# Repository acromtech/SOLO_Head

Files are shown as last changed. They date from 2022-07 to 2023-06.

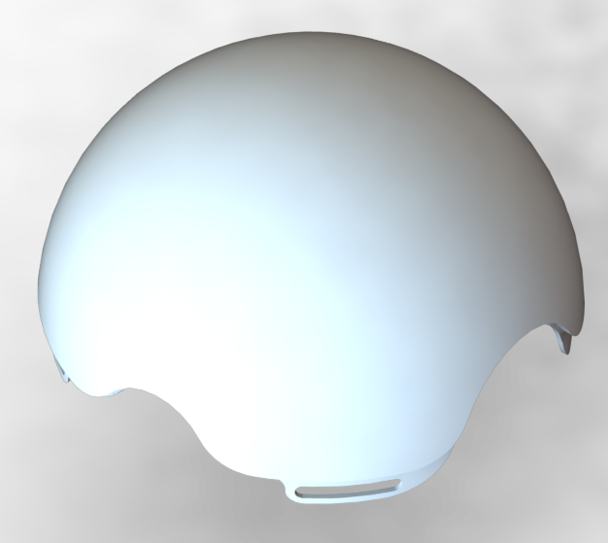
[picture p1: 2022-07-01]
SOLO_HEAD_1DOF_V6/IMAGES/Head_Top.png

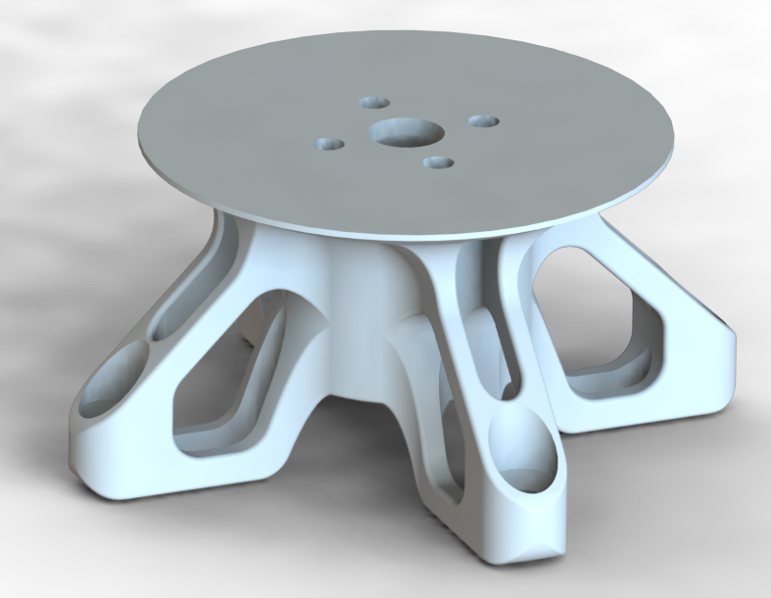
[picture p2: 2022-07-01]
SOLO_HEAD_1DOF_V6/IMAGES/SH06-Head_Stand.png

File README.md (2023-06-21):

# SOLO_Head

## Assembly
Solo_Head
<br>*Note : Equations can be used to re-size head diameter*

## Design Parts
| CAO | Print | Printing time | Name | Filament | Comment |
|:---:|:---:|---|---|---|---|
|  |  | 9h | 1x Head_Top | ABS | 45° touching buildplate supports required (use soluble supports is better) |
|  | | 1min | 1x Head_Joint | Neoprene | made with laser cutter machine |
|  || 33min | 2x Microphone_Joint | TPU | 45° touching buildplate supports required (use soluble supports is better) |
|  || 20min | 4x Camera_Spacer<br>4x CM4_Spacer<br>8x uDriver_Spacer | ABS | No support required |
|  |  | 1h | 1x Board_Mount | ABS | No support required |
|  |  | 5min | 1x End_Stop | ABS | No support required |
|  | | 1h30 | 1x Encoder_Mount | ABS | No support required |
|  |  | 20min | 1x Encoder_Adaptator | ABS | No support required |
|  |  | 12h | 1x Head_Bottom | ABS | 45° touching buildplate supports required (use soluble supports is better) |
|  || 4h | 1x Head_Stand | ABS | No support required but print with soluble support is better |

## Generic Parts
| Screen | Reference | Link | Comment |
|:---:|---|---|---|
||1x 6700-2RS ball bearing<br>Ø10xØ15x4mm|[123Roulement](https://www.123roulement.com/roulements-6700-2RS)|To link "Encoder_Mount" and "Encoder_Adaptator" design parts|
||8x TCHC M3x8 Screw|[Fixnvis](https://www.visseriefixations.fr/vis-a-six-pans-creux/tete-fraisee-hexagonale-creuse/inox-a4/tfhc-m3x8-inox-a4-ef-din-7991.html)|To link "Encoder_Mount" design part and the motor<br>To link "Encoder_Mount" and "Head_Bottom" design parts|
||4x TCHC M2.5x20 Screw|[Fixnvis](https://www.visseriefixations.fr/vis-a-six-pans-creux/tete-fraisee-hexagonale-creuse/inox-a4/tfhc-m2-5x20-inox-a4-din-7991.html)|To link "Board_Mount" with spacers and "Head_Bottom" design parts|
||1x AEDB-9140-A13 Broadcom Encoder|[RS](https://fr.rs-online.com/web/p/codeurs/7967806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)|/|
||1x GB4106 Tmotor motor|[Hexadrone](https://hexadrone.fr/gamme-gimbal-nacelle/509-moteur-brushless-nacelle-gb4106-tmotor-6971360351184.html)|/|
||1x Arducam 2MP Global Shutter OG02B10 Pivariety camera module |[Robotshop](https://www.robotshop.com/be/fr/module-camera-couleur-arducam-2mp-global-shutter-og02b10-pivariety.html)|/|
||1x ArduCam M12 camera lens (6pcs)|[Robotshop](https://www.robotshop.com/be/fr/kit-objectif-arducam-m12-pour-camera-hq-20-180deg-6pcs.html)|/|
||1x CM4 Raspberry Pi|[Kubii](https://www.kubii.fr/cartes-raspberry-pi/3086-raspberry-pi-compute-module-4-3272496302952.html)|/|
||2x Microphone module|/|Electronic CAD are in the repository "hardware"|
||2x uDriver board||[ODRI repository](https://github.com/open-dynamic-robot-initiative/open_robot_actuator_hardware/blob/master/electronics/micro_driver_electronics/README.md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)|
||2x DF13-5S-1.25C Hirose connector|[RS components](https://fr.rs-online.com/web/p/boitiers-de-connecteurs-pour-circuits-imprimes/1113616)|To link uDriver and communication cables<br>To link CM4 Raspberry Pi and communication cables|
||1x DF13-5P-1.25DS Hirose connector|[RS components](https://fr.rs-online.com/web/p/embases-circuits-imprimes/7793529)|To change encoder connector|
||1x DF13-5P-1.25DSA Hirose connector|[RS components](https://fr.rs-online.com/web/p/embases-circuits-imprimes/5037912)|To link head CM4 Raspberry Pi shield communication cables to body Raspberry Pi communication cables|
||1x RE-6619107 XT30U 2 mm Reely Male  connector|[Conrad](https://www.conrad.fr/p/reely-re-6619107-fiche-male-pour-batterie-xt30u-2-mm-femelle-doree-a-souder-1-pcs-2206369)|To link power cables to uDriver board|
||1x RE-6619104 XT30U 2 mm Reely Female connector|[Conrad](https://www.conrad.fr/p/reely-re-6619107-fiche-male-pour-batterie-xt30u-2-mm-femelle-doree-a-souder-1-pcs-2206369)|To link power cables to power board (on SOLO body)|
||1x Kabeltronik 160110009-1 1mm² Black Power Wire|[Conrad](https://www.conrad.com/p/kabeltronik-160110009-1-strand-lify-1-x-1-mm-black-sold-per-metre-323735)|To power uDriver board|
||1x Kabeltronik 160110008 1mm² Red Power Wire|[Conrad](https://www.conrad.fr/p/fil-de-cablage-lify-kabeltronik-160110008-1-1-x-1-mm-rouge-marchandise-vendue-au-metre-323734)|To power uDriver board|
||1x 10 way 3M 3302-10 100FT communication cables |[RS components](https://fr.rs-online.com/web/p/cables-en-nappe/1055281)|To link encoder and uDriver (5 way)<br>To link CM4 Raspberry Pi and uDriver (5 way)|
||1x DF13-2630SCF 0.12mm² Hirose DF13 Crimp Terminals|[RS components](https://fr.rs-online.com/web/p/cables-en-nappe/1055281)|To link communication cables with DF13-5S-1.25C Hirose connector|
||1x DF13-TB2630HC Hirose Crimping Tool for DF13 Crimp Terminals |[RS components](https://fr.rs-online.com/web/p/cables-en-nappe/1055281)|To link communication cables with DF13-5S-1.25C Hirose connector|

## Next Version (V7)
To reduce mass, clean print, and keep design apparence. I realize some modifications on the V6 design :
* Delete "Head_Joint" neoprene gasket and chamfer "Head_Bottom" and "Head_Top" parts to simplify the model and clean model surface.
* Design a new "Head_Stand" to link the SOLO's head to SOLO's body.
* Delete "Microphone_Joint" and integrate a screwing system on "Head_Bottom" to simplify the model. To limit microphone noise, generic O-rings are positioned on the screw.
* Upgrade clips shape to limit printing supports.

## License
BSD 3-Clause License

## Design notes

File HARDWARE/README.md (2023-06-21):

# Hardware

## Features
Quantity|Reference|Voltage [V]|Intensity [A]|Detail
---|---|---|---|---|
1|[SLS X-Cube 850mAh lithium polymer batteries](https://github.com/open-dynamic-robot-initiative/open_robot_actuator_hardware/blob/master/mechanics/quadruped_robot_12dof_v1.1/README.md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)|24(2x3S)|30C continous = 2 x 30 x 0.85 = 51<br>60C burst = 2 x 60 x 0.85 = 102 |/|
1|[uDriverv2](https://github.com/open-dynamic-robot-initiative/open_robot_actuator_hardware/tree/master/electronics/micro_driver_electronics)|5-32|/|/|
2|[IPower GM2804 (+ AS5048A encoder)](https://www.robotshop.com/ca/fr/moteur-cardan-ipower-gm2804-avec-encodeur-as5048a.html)|10|0.07-5|Hollow shaft diameter : 5.7mm <br> [Drawings](https://user-images.githubusercontent.com/103576080/168556596-d6f692c8-2cbd-48c1-b92e-5072b6c10471.jpg) <br> Resistance : 5.57Ω|
2|[AEDB-9140-A13 optical encoder](https://fr.rs-online.com/web/p/codeurs/7967806)|(-0.5)-7|0.001-0.018|/|
2|[I2S MEMS (MicroElectroMechanical Systems) microphone for Raspberry Pi](https://makersportal.com/shop/i2s-mems-microphone-for-raspberry-pi-inmp441)|/|/|/|
1|[Arducam OG02B10 2MP Global Shutter color camera module](https://www.arducam.com/product/arducam-2mp-og02b10-global-shutter-color-camera-modules-for-raspberry-pi/)|/|/|/|
1 | Raspberry Pi CM4|5|3|/|

## Minimum power wires section
Raspberry Pi 4 maximum intensity + Motor maximum intensity = 8A

>S = (ρ x 2L x I)/U’ = 0.021 x 2 x 8 / (24 x 0.3) = 0.46mm²<br>S = (ρ x 2L x I)/U’ = 0.021 x 2 x 8 / (48 x 0.3) = 0.23mm²

Unit | Detail |
--- | --- |
ρ | coper resistance = 0.021|
L | cable length (go+back)|
I | system intensity|
U' | voltage drop = system voltage x 3%|

So, for a 24V battery voltage, a battery intensity max of 8A and a 1m cable length (2m in the up table) a 0.5mm² cable section be sufficient. Usualy 0.5mm² section cable have ~Ø2.6mm outer diameter. 
>Currently 1mm² section are used on SOLO quadruped robot to power legs uDriverv2.

## Raspberry Pi communication wires
Self-made ethernet wire with 4 connections|Robot interface wire|
---|---|
ethernet_connector | connection_wire_2
> Four RS 180-6028 wires (0.14mm²/~Ø1.5mm) are fixed to the ethernet connector ([more informations](https://github.com/open-dynamic-robot-initiative/open_robot_actuator_hardware/blob/master/electronics/details/details_wiring.md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))

## SOLO head wire
>Hollow shaft superficy : π(5.7/2)² = 25.52mm² <br> Wire superficy : 2π(2.6/2)² + 4π(1.5/2)² = 17.69mm²

17.69mm² < 25.52mm² => OK

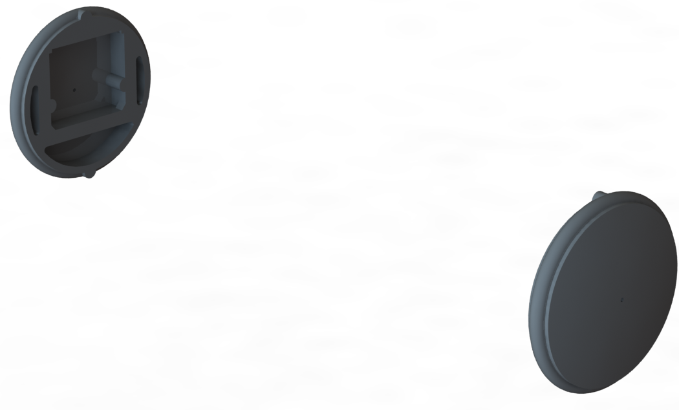
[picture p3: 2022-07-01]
SOLO_HEAD_1DOF_V6/IMAGES/Microphone_Joint.png

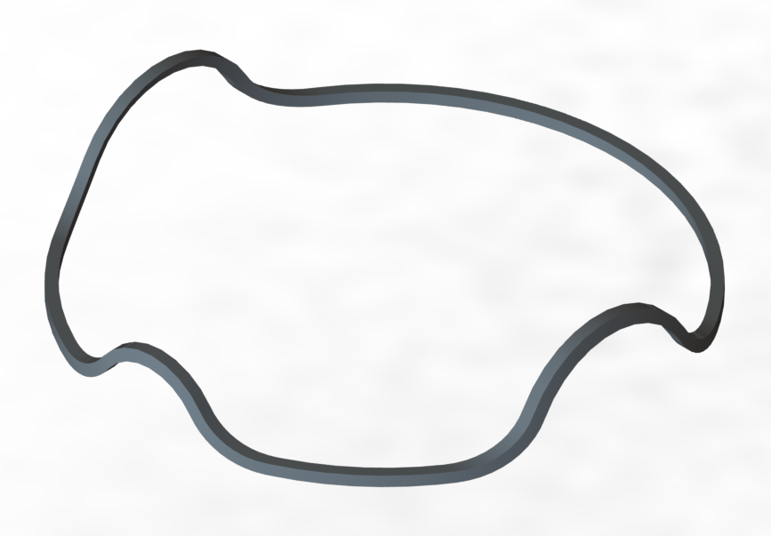
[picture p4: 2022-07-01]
SOLO_HEAD_1DOF_V6/IMAGES/Joint.png

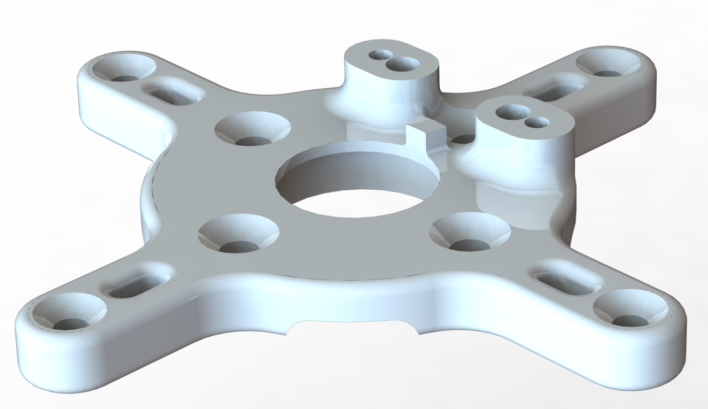
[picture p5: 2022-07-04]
SOLO_HEAD_1DOF_V6/IMAGES/Encoder_Mount.png

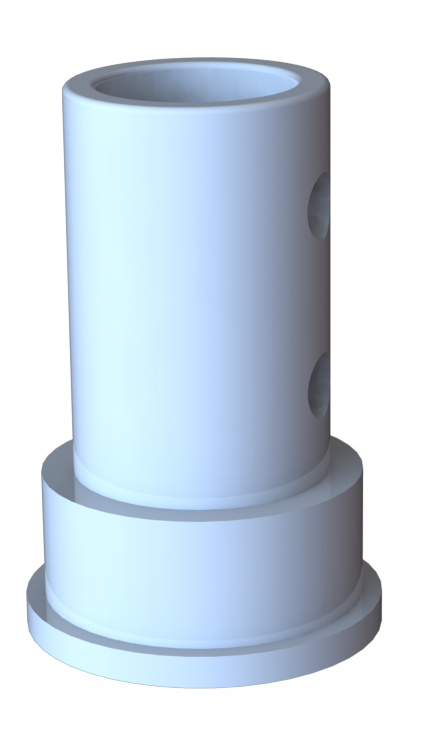
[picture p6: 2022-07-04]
SOLO_HEAD_1DOF_V6/IMAGES/Encoder_Adaptator.png

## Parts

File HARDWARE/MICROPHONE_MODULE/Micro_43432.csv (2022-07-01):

Id | Designator | Package | Quantity | Designation | Supplier and ref
1 | C1 | C_0402_1005Metric | 1 | 0.1u
2 | J1 | Hirose_DF13-06P-1.25DSA_1x06_P1.25mm_Vertical | 1 | Conn_01x06_Female
3 | R1 | R_01005_0402Metric_Pad0.57x0.30mm_HandSolder | 1 | 100k
4 | K1 | MIC_ICS-43432 | 1 | ICS-43432

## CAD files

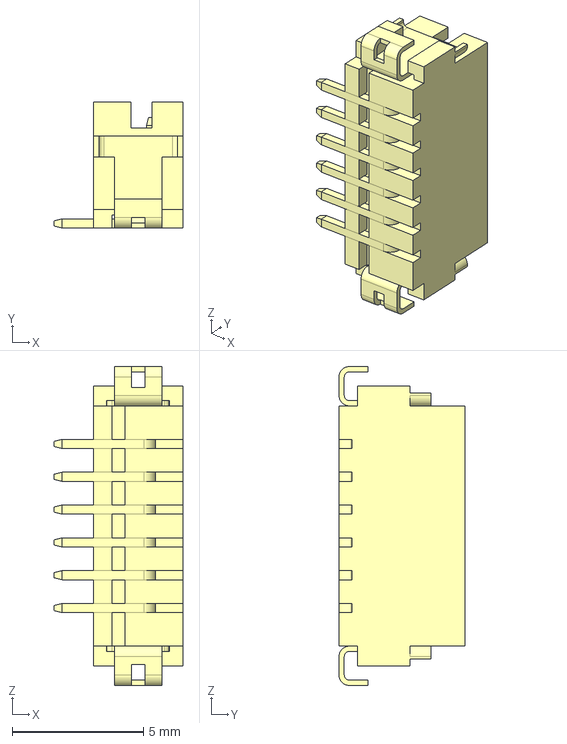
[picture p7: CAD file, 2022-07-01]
HARDWARE/MICROPHONE_MODULE/DF13C-6P-1.25V(21)_CL0536-0405-3-21_3DDrawing_STEP_0001217384S/WNCW-1600327.stp
4.90 x 4.80 x 12.2 mm

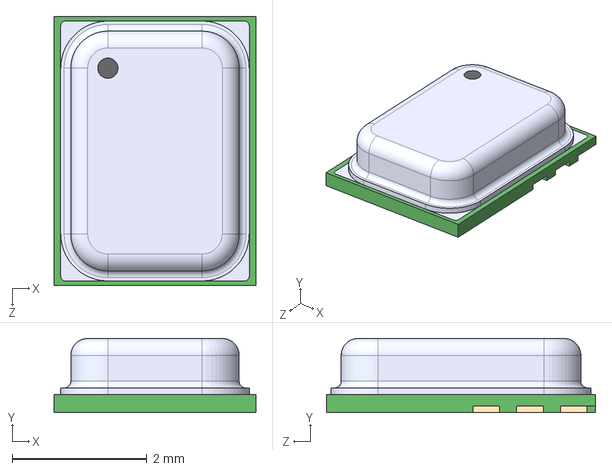
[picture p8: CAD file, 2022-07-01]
HARDWARE/MICROPHONE_MODULE/ICS-43432/ICS-43432.step
3.00 x 1.10 x 4.00 mm

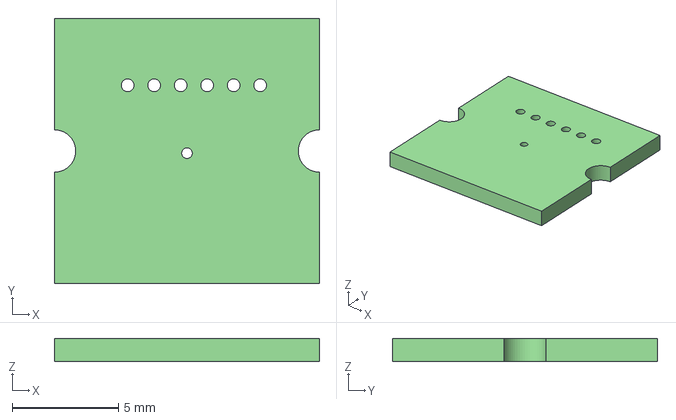
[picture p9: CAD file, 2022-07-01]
HARDWARE/MICROPHONE_MODULE/Micro_43432.step
12.5 x 12.5 x 1.09 mm

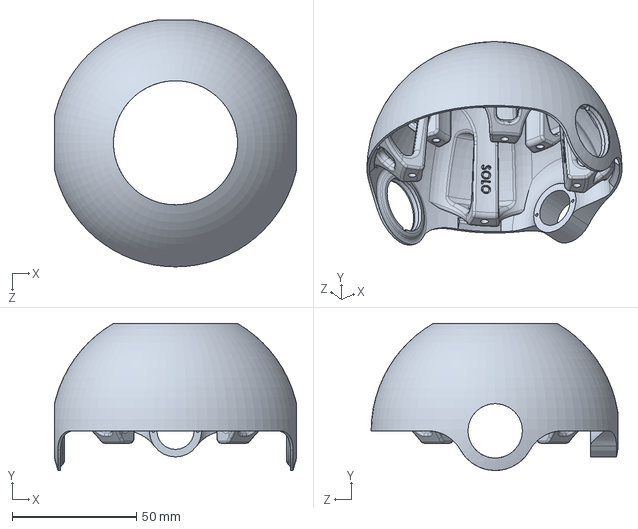
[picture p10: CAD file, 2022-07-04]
SOLO_HEAD_1DOF_V6/SOLIDWORKS_ASSEMBLY/SH06-Head_Bottom.SLDPRT
97.5 x 59.3 x 99.4 mm

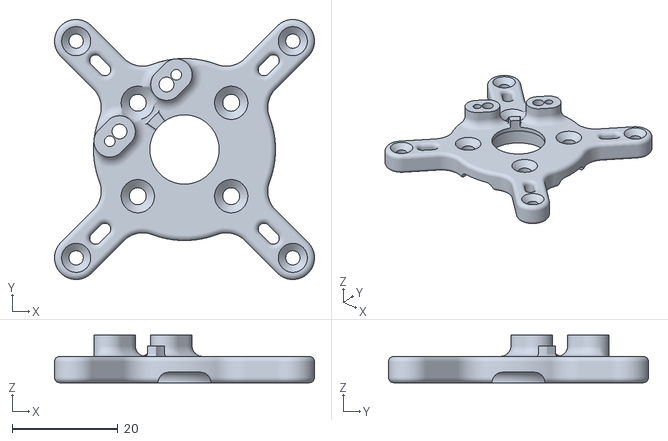
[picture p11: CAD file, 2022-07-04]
SOLO_HEAD_1DOF_V6/STL/SH06-Encoder_Mount_V2.STL
49.2 x 49.2 x 9.00

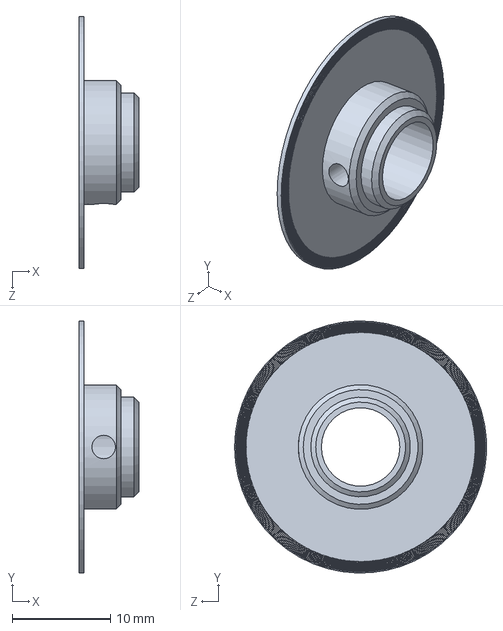
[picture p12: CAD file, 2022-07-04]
SOLO_HEAD_1DOF_V6/SOLIDWORKS_ASSEMBLY/SH06-zz_AEDB-9140-A13_broadcom_encoder_wheel.SLDPRT
6.08 x 25.7 x 25.7 mm

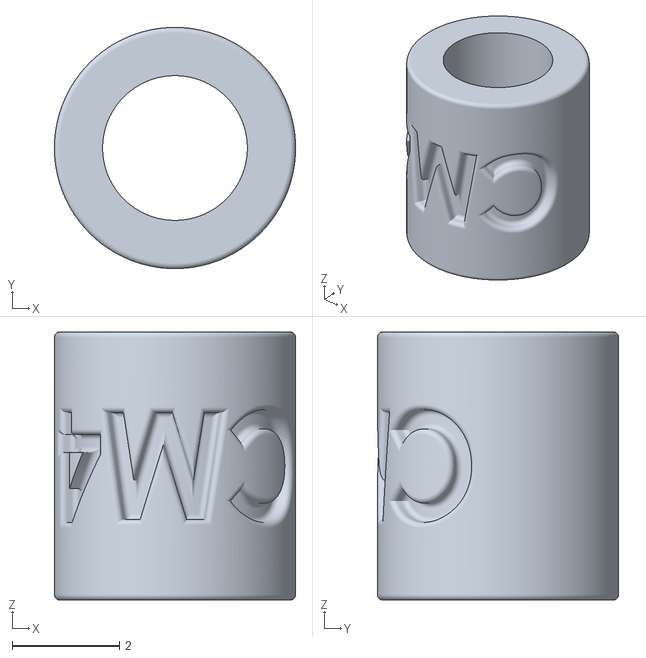
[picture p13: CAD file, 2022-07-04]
SOLO_HEAD_1DOF_V6/STL/SH06-Shield_CM4_Spacer.STL
4.50 x 4.50 x 5.00

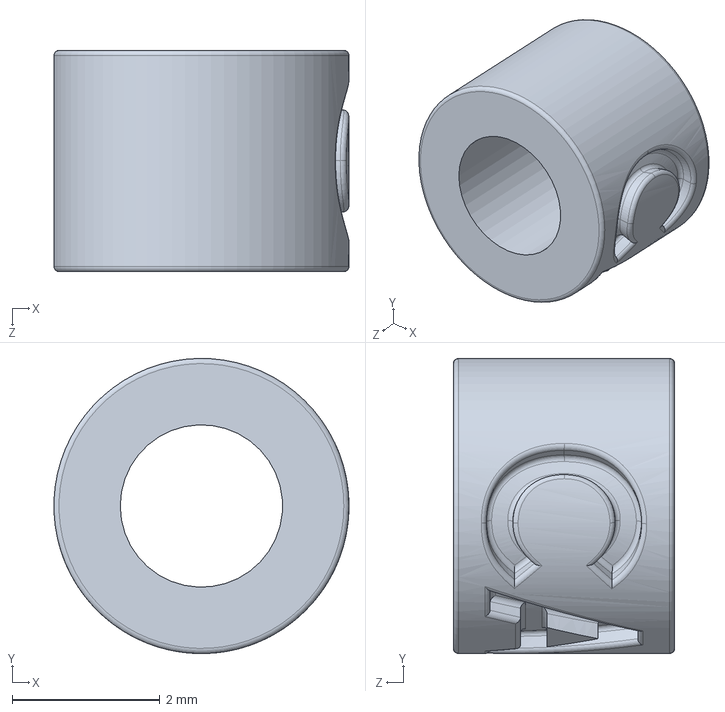
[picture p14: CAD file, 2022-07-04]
SOLO_HEAD_1DOF_V6/SOLIDWORKS_ASSEMBLY/SH06-Camera_Module_Spacer.SLDPRT
4.00 x 4.00 x 3.00 mm

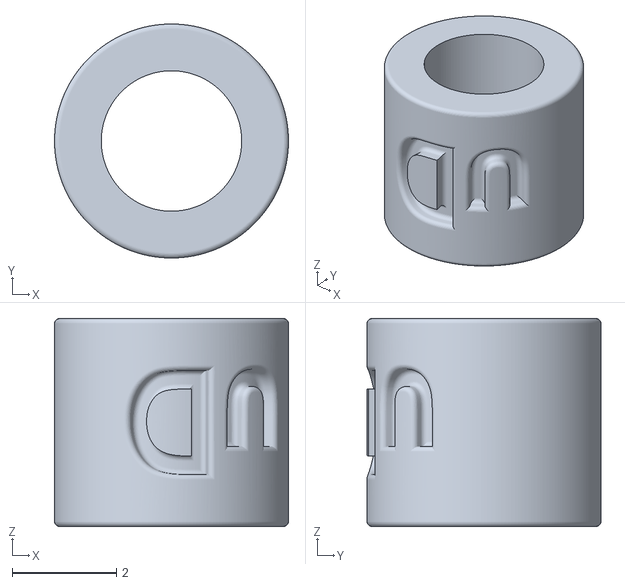
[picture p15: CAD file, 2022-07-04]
SOLO_HEAD_1DOF_V6/STL/SH06-uDriver_Spacer.STL
4.50 x 4.50 x 4.00

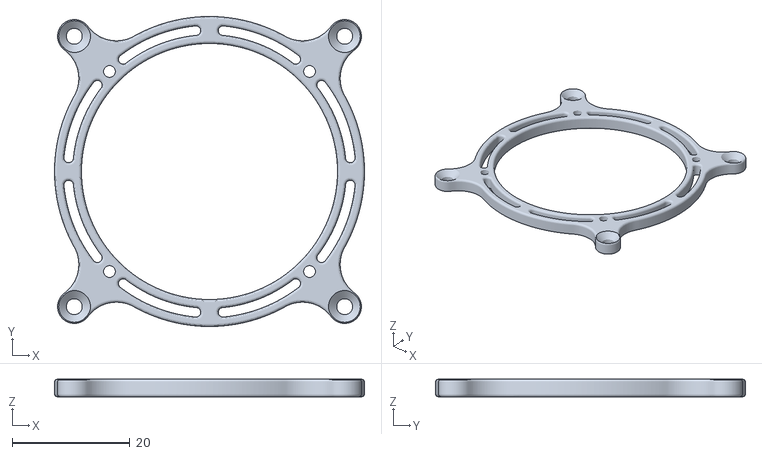
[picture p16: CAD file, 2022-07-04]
SOLO_HEAD_1DOF_V6/STL/SH06-Boards_Mount.STL
52.7 x 52.7 x 3.00

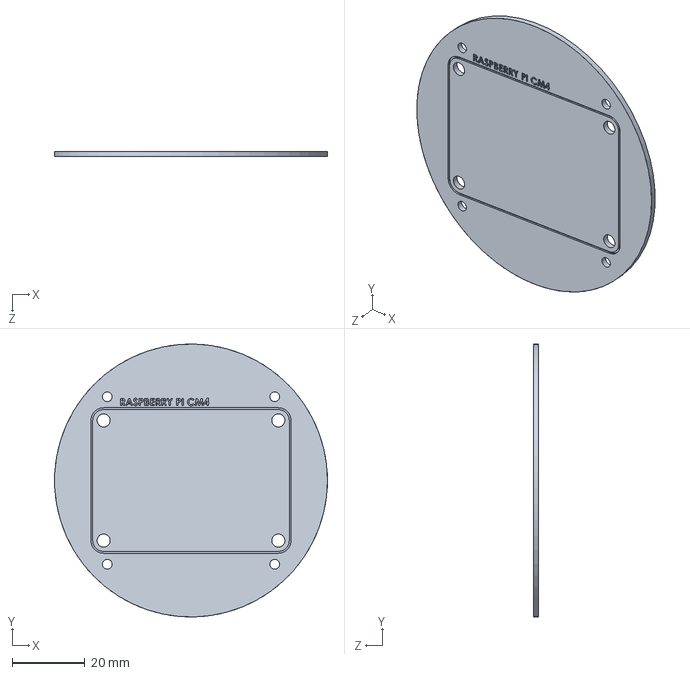
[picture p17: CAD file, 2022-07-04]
SOLO_HEAD_1DOF_V6/SOLIDWORKS_ASSEMBLY/SH06-Shield_CM4_Footprint.SLDPRT
75.0 x 75.0 x 1.50 mm

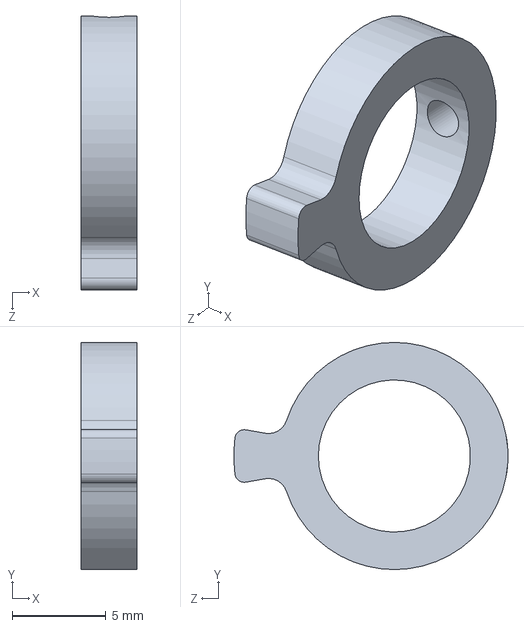
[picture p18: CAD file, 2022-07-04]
SOLO_HEAD_1DOF_V6/SOLIDWORKS_ASSEMBLY/SH06-End_Stop.SLDPRT
3.00 x 12.1 x 14.6 mm

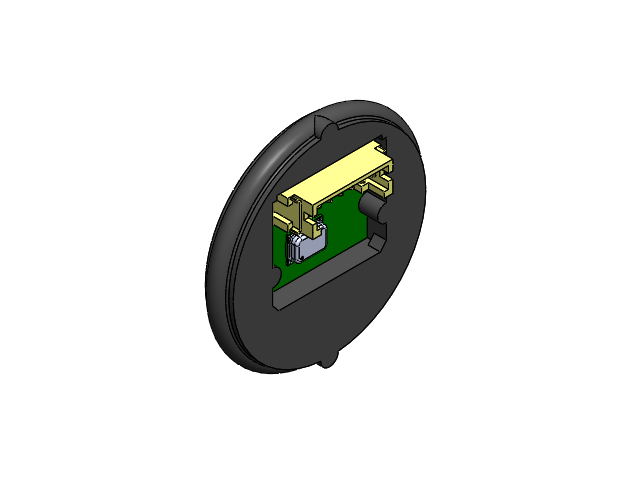
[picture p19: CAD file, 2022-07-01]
SOLO_HEAD_1DOF_V6/SOLIDWORKS_ASSEMBLY/SH06-01-MICROPHONE_MODULE_V3.SLDASM
SH06-Microphone_Joint_V3
SH06-zz_laas_microphone_v3

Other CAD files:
SOLO_HEAD_1DOF_V6/SOLIDWORKS_ASSEMBLY/SH06-uDriver_Spacer.SLDPRT
SOLO_HEAD_1DOF_V6/STL/SH06-Shield_CM4_Footprint.STL
SOLO_HEAD_1DOF_V6/STL/SH06-Camera_Module_Spacer.STL
SOLO_HEAD_1DOF_V6/SOLIDWORKS_ASSEMBLY/SH06-Encoder_Mount_V2.SLDPRT
HARDWARE/MICROPHONE_MODULE/Micro_43432_no_screw.step
SOLO_HEAD_1DOF_V6/DXF/SH06-Head_Joint_V4.DXF
SOLO_HEAD_1DOF_V6/SOLIDWORKS_ASSEMBLY/SH06-Boards_Mount.SLDPRT
SOLO_HEAD_1DOF_V6/SOLIDWORKS_ASSEMBLY/SH06-Encoder_Adaptator_V2.SLDPRT
SOLO_HEAD_1DOF_V6/SOLIDWORKS_ASSEMBLY/SH06-Head_Joint_V4.SLDPRT
SOLO_HEAD_1DOF_V6/SOLIDWORKS_ASSEMBLY/SH06-Head_Stand.SLDPRT
SOLO_HEAD_1DOF_V6/SOLIDWORKS_ASSEMBLY/SH06-Head_Top_V2.SLDPRT
SOLO_HEAD_1DOF_V6/SOLIDWORKS_ASSEMBLY/SH06-Microphone_Joint_V3.SLDPRT
SOLO_HEAD_1DOF_V6/SOLIDWORKS_ASSEMBLY/SH06-Shield_CM4_Spacer.SLDPRT
SOLO_HEAD_1DOF_V6/SOLIDWORKS_ASSEMBLY/SH06-zz_AEDB-9140-A13_broadcom_encoder.SLDPRT
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

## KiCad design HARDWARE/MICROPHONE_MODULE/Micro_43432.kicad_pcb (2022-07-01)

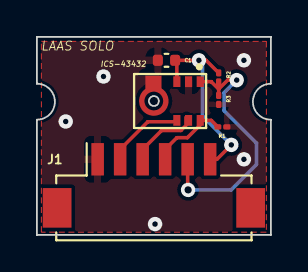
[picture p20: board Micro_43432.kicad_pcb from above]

Board: 2 copper layers, 13.0 x 11.0 mm, 6 parts (0 on the bottom side), 6 nets.

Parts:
C1: 0.1u; C_0402_1005Metric
J1: Conn_01x06_Female; Hirose_DF13C_CL535-0406-3-51_1x06-1MP_P1.25mm_Vertical
K1: ICS-43432; MIC_ICS-43432
R1: 100k; R_01005_0402Metric
R2: NC; R_01005_0402Metric
R3: 0; R_01005_0402Metric

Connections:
/LR: J1.5, K1.1 (LR), R2.2, R3.1
/SCK: J1.3, K1.6 (SCK)
/SD: J1.4, K1.7 (SD), R1.1
/WS: J1.2, K1.5 (WS)
GND: C1.2, J1.1, K1.2 (CONFIG), K1.4 (GND), R1.2, R3.2
VDD: C1.1, J1.6, K1.3 (VDD), R2.1

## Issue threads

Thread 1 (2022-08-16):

Aurélien Solidwork problèmes

ox6d, 2022-08-16:
Salut,

tes fichiers solidworks ont été crées à partir de quel version de SLD ? Car j'ai tenté de les ouvrir mais impossible de le faire ( j'ai SLD 2019) . Du coup j'ai ouvert sur onshape mais du coup impossible de modifier les équations de la tete.
Merci d'avance :)
Voila voila .

A.BENOIT

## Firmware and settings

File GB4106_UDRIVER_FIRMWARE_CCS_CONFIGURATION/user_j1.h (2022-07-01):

/*
 * ===========================================================================
 * This file contains configuation for the motor on J1 when using SINGLE MOTOR
 * applications.
 * ===========================================================================
 *
 */
#ifndef _USER_J1_H_
#define _USER_J1_H_
/* --COPYRIGHT--,BSD
 * Copyright (c) 2015, Texas Instruments Incorporated
 * Copyright (c) 2019, Max Planck Gesellschaft, New York University
 * All rights reserved.
 *
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
 * *  Redistributions of source code must retain the above copyright
 *    notice, this list of conditions and the following disclaimer.
 *
 * *  Redistributions in binary form must reproduce the above copyright
 *    notice, this list of conditions and the following disclaimer in the
 *    documentation and/or other materials provided with the distribution.
 *
 * *  Neither the name of Texas Instruments Incorporated nor the names of
 *    its contributors may be used to endorse or promote products derived
 *    from this software without specific prior written permission.
 *
 * THIS SOFTWARE IS PROVIDED BY THE COPYRIGHT HOLDERS AND CONTRIBUTORS "AS IS"
 * AND ANY EXPRESS OR IMPLIED WARRANTIES, INCLUDING, BUT NOT LIMITED TO,
 * THE IMPLIED WARRANTIES OF MERCHANTABILITY AND FITNESS FOR A PARTICULAR
 * PURPOSE ARE DISCLAIMED. IN NO EVENT SHALL THE COPYRIGHT OWNER OR
 * CONTRIBUTORS BE LIABLE FOR ANY DIRECT, INDIRECT, INCIDENTAL, SPECIAL,
 * EXEMPLARY, OR CONSEQUENTIAL DAMAGES (INCLUDING, BUT NOT LIMITED TO,
 * PROCUREMENT OF SUBSTITUTE GOODS OR SERVICES; LOSS OF USE, DATA, OR PROFITS;
 * OR BUSINESS INTERRUPTION) HOWEVER CAUSED AND ON ANY THEORY OF LIABILITY,
 * WHETHER IN CONTRACT, STRICT LIABILITY, OR TORT (INCLUDING NEGLIGENCE OR
 * OTHERWISE) ARISING IN ANY WAY OUT OF THE USE OF THIS SOFTWARE,
 * EVEN IF ADVISED OF THE POSSIBILITY OF SUCH DAMAGE.
 * --/COPYRIGHT--*/

//! \file
//! \brief Contains the public interface for user initialization data for the CTRL, HAL, and EST modules 
//!
//! (C) Copyright 2015, Texas Instruments, Inc.
//! (C) Copyright 2019, Max Planck Gesellschaft, New York University


// **************************************************************************
// the includes

//!
//!
//! \defgroup USER USER
//!
//@{


#ifdef __cplusplus
extern "C" {
#endif

// **************************************************************************
// the defines

//! \brief CURRENTS AND VOLTAGES
// **************************************************************************
//! \brief Defines the full scale frequency for IQ variable, Hz
//! \brief All frequencies are converted into (pu) based on the ratio to this value
//! \brief this value MUST be larger than the maximum speed that you are expecting from the motor
#ifndef QEP
#define USER_IQ_FULL_SCALE_FREQ_Hz        (800.0)   // 800 Example with buffer for 8-pole 6 KRPM motor to be run to 10 KRPM with field weakening; Hz =(RPM * Poles) / 120
#else
//#define USER_IQ_FULL_SCALE_FREQ_Hz        (USER_MOTOR_NUM_POLE_PAIRS/0.008)   // (4/0.008) = 500 Example with buffer for 8-pole 6 KRPM motor to be run to 6 KRPM; Hz = (RPM * Poles) / 120
#define USER_IQ_FULL_SCALE_FREQ_Hz        (1310.0)   // value given by the excel spreadsheet
#endif

//! \brief Defines full scale value for the IQ30 variable of Voltage inside the system
//! \brief All voltages are converted into (pu) based on the ratio to this value
//! \brief WARNING: this value MUST meet the following condition: USER_IQ_FULL_SCALE_VOLTAGE_V > 0.5 * USER_MOTOR_MAX_CURRENT * USER_MOTOR_Ls_d * USER_VOLTAGE_FILTER_POLE_rps,
//! \brief WARNING: otherwise the value can saturate and roll-over, causing an inaccurate value
//! \brief WARNING: this value is OFTEN greater than the maximum measured ADC value, especially with high Bemf motors operating at higher than rated speeds
//! \brief WARNING: if you know the value of your Bemf constant, and you know you are operating at a multiple speed due to field weakening, be sure to set this value higher than the expected Bemf voltage
//! \brief It is recommended to start with a value ~3x greater than the USER_ADC_FULL_SCALE_VOLTAGE_V and increase to 4-5x if scenarios where a Bemf calculation may exceed these limits
//! \brief This value is also used to calculate the minimum flux value: USER_IQ_FULL_SCALE_VOLTAGE_V/USER_EST_FREQ_Hz/0.7
#define USER_IQ_FULL_SCALE_VOLTAGE_V      (24.0)   // 24.0 Set to Vbus

//! \brief Defines the maximum voltage at the input to the AD converter
//! \brief The value that will be represented by the maximum ADC input (3.3V) and conversion (0FFFh)
//! \brief Hardware dependent, this should be based on the voltage sensing and scaling to the ADC input
#define USER_ADC_FULL_SCALE_VOLTAGE_V       (44.30)  // BOOSTXL-DRV8305EVM = 44.30 V

//! \brief Defines the full scale current for the IQ variables, A
//! \brief All currents are converted into (pu) based on the ratio to this value
//! \brief WARNING: this value MUST be larger than the maximum current readings that you are expecting from the motor or the reading will roll over to 0, creating a control issue 
#define USER_IQ_FULL_SCALE_CURRENT_A         (24.0) // BOOSTXL-DRV8305EVM = 24.0 A

//! \brief Defines the maximum current at the AD converter
//! \brief The value that will be represented by the maximum ADC input (3.3V) and conversion (0FFFh)
//! \brief Hardware dependent, this should be based on the current sensing and scaling to the ADC input
#define USER_ADC_FULL_SCALE_CURRENT_A        (47.14)  // BOOSTXL-DRV8305EVM = 47.14 A

//! \brief Defines the number of current sensors used
//! \brief Defined by the hardware capability present
//! \brief May be (2) or (3)
#define USER_NUM_CURRENT_SENSORS            (3)   // 3 Preferred setting for best performance across full speed range, allows for 100% duty cycle

//! \brief Defines the number of voltage (phase) sensors
//! \brief Must be (3)
#define USER_NUM_VOLTAGE_SENSORS            (3) // 3 Required

//! \brief ADC current offsets for A, B, and C phases
//! \brief One-time hardware dependent, though the calibration can be done at run-time as well
//! \brief After initial board calibration these values should be updated for your specific hardware so they are available after compile in the binary to be loaded to the controller
//#define   I_A_offset    (1.20)
//#define   I_B_offset    (1.20)
//#define   I_C_offset    (1.20)
#define   I_A_offset    (1.004728198)
#define   I_B_offset    (1.005483985)
#define   I_C_offset    (1.006817698)

//! \brief ADC voltage offsets for A, B, and C phases
//! \brief One-time hardware dependent, though the calibration can be done at run-time as well
//! \brief After initial board calibration these values should be updated for your specific hardware so they are available after compile in the binary to be loaded to the controller
#define   V_A_offset    (0.4910094738)
#define   V_B_offset    (0.4885113835)
#define   V_C_offset    (0.4871017337)
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

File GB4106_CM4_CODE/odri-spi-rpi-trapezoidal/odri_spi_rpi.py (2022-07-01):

#!/usr/bin/env python3

#Thomas Flayols - feb 2022
#https://github.com/thomasfla/odri-spi-rpi
#https://github.com/open-dynamic-robot-initiative/master-board/blob/master/documentation/BLMC_%C2%B5Driver_SPI_interface.md
import struct
import spidev
import RPi.GPIO as GPIO
import spidev
from IPython import embed
from math import pi
import time
def crc32(buf):
  crc=0xffffffff
  for val in buf:
    crc ^= val << 24
    for _ in range(8):
      crc = crc << 1 if (crc & 0x80000000) == 0 else (crc << 1) ^ 0x104c11db7
  return crc

def checkcrc(buf):
  crc = crc32(buf[:-4])
  if (crc&0xffff == buf[-4]*256+buf[-3] and (crc&0xFFFF0000)>>16 == buf[-2]*256+buf[-1] ): #todo, clean
    return True
  return False

class SPIuDriver:
  def __init__(self, waitForInit = True, absolutePositionMode = False, offsets=[0.0,0.0]):

    #Configure CS pin
    GPIO.setmode(GPIO.BCM)
    GPIO.setup(25,GPIO.OUT)
    GPIO.output(25,0)

    #Initialise SPI
    self.spi = spidev.SpiDev()
    self.spi.open(0, 0)
    self.spi.mode=0
    self.spi.max_speed_hz = 8000000

    # Allocate all variables
    self.is_system_enabled = 0
    self.error_code = 0
    self.position0 = 0
    self.position1 = 0
    self.velocity0 = 0
    self.velocity1 = 0
    self.current0 = 0
    self.current1 = 0
    self.is_enabled0 = 0
    self.is_enabled1= 0
    self.is_ready0 = 0
    self.is_ready1 = 0
    self.has_index_been_detected0 = 0
    self.has_index_been_detected1 = 0
    self.index_toggle_bit0 = 0
    self.index_toggle_bit1 = 0

    self.offset0 = offsets[0]
    self.offset1 = offsets[1]

    self.EI1OC = 1 if absolutePositionMode else 0
    self.EI2OC = 1 if absolutePositionMode else 0
    self.refPosition0 = 0
    self.refPosition1= 0
    self.refVelocity0= 0
    self.refVelocity1= 0
    self.refCurrent0= 0
    self.refCurrent1= 0
    self.iSatCurrent0= 0
    self.iSatCurrent1= 0
    self.kp0= 0
    self.kp1= 0
    self.kd0= 0
    self.kd1= 0
    self.timeout = 50

    self.error = -1
    #wait for system enable
    if waitForInit:
      print(">> Calibrating motor, please wait")
      while(not self.is_ready0):
        self.transfer()
        time.sleep(0.001)
    print(">> Waiting for index pulse to have absolute position reference, please move the motor manualy")
    if absolutePositionMode:
      while(not self.has_index_been_detected0): #or not self.has_index_been_detected1):
        self.transfer()
        time.sleep(0.001)
    print ("ready!")
  def transfer(self):

    #generate command packet
    ES = 1
    EM1 = 1	
    EM2	= 1
    EPRE = 0
    EI1OC = self.EI1OC
    EI2OC	= self.EI2OC
    mode = (ES << 7) | (EM1 << 6) | (EM2<<5)|(EPRE<<4)|(EI1OC<<3)|(EI2OC<<2)
    timeout = self.timeout
    rawRefPos0 = int((self.refPosition0-self.offset0)/(2.*pi)*(1<<24) )
    rawRefPos1 = int((self.refPosition1-self.offset1)/(2.*pi)*(1<<24))
    rawRefVel0 = int(self.refVelocity0*(1<<11)*60.0/(2000*pi))
    rawRefVel1 = int(self.refVelocity1*(1<<11)*60.0/(2000*pi))
    rawRefIq0 = int(self.refCurrent0*(1<<10))
    rawRefIq1 = int(self.refCurrent1*(1<<10))
    rawIsat0 = int(self.iSatCurrent0*(1<<3))
    rawIsat1 = int(self.iSatCurrent1*(1<<3))
    rawKp0 = int(self.kp0*(1<<11)*(2*pi) )
    rawKp1 = int(self.kp1*(1<<11)*(2*pi) )
    rawKd0 = int(self.kd0*(1<<10)*(2*pi*1000./60.0) )
    rawKd1 = int(self.kd1*(1<<10)*(2*pi*1000./60.0) )
    commandPacket = bytearray(struct.pack(">BBiihhhhHHHHBBHI",mode,timeout,rawRefPos0,rawRefPos1,rawRefVel0,rawRefVel1,rawRefIq0,rawRefIq1,rawKp0,rawKp1,rawKd0,rawKd1, rawIsat0, rawIsat1, 0,0))
    crc=crc32(commandPacket[:-4])
    commandPacket[-4]=(crc>>24)&0xff
    commandPacket[-3]=(crc>>16)&0xff
    commandPacket[-2]=(crc>>8)&0xff
    commandPacket[-1]=(crc)&0xff
    GPIO.output(25,0) #enable CS
    sensorPacket = bytearray(self.spi.xfer(commandPacket))
    GPIO.output(25,1) #disable CS
    #print(commandPacket.hex(),checkcrc(commandPacket))
    #print(sensorPacket.hex(),checkcrc(sensorPacket))
    if checkcrc(sensorPacket):
    #decode received sensor packet
      data = struct.unpack(">H H i i h h h h xxxxxxxxxxxxxx",sensorPacket)
      self.is_system_enabled        = data[0]&0b1000000000000000 != 0
      self.is_enabled0              = data[0]&0b0100000000000000 != 0
      self.is_ready0                = data[0]&0b0010000000000000 != 0
      self.is_enabled1              = data[0]&0b0001000000000000 != 0
      self.is_ready1                = data[0]&0b0000100000000000 != 0
      self.has_index_been_detected0 = data[0]&0b0000010000000000 != 0
      self.has_index_been_detected1 = data[0]&0b0000001000000000 != 0

      self.error             = data[0]&0b0000000000001111
      self.position0 = data[2] / (1<<24) * 2.0 * pi + self.offset0
      self.position1 = data[3] / (1<<24) * 2.0 * pi + self.offset1
      self.velocity0 = data[4] / (1<<11) * 2000*pi/60.0
      self.velocity1 = data[5] / (1<<11) * 2000*pi/60.0
      self.current0 = data[6]  / (1<<10)
      self.current1 = data[7]  / (1<<10)
      #print("velocity =", self.velocity0)
      #print("cur =", self.current0)
    else:
        raise(Exception(f"Error: sensor frame is corrupted is uDriver powered on?"))
    if (self.error!=0):
        raise(Exception(f"Error from motor driver: Error {self.error}"))

  def goto(self,p0,p1):
        p0_start = self.position0
        p1_start = self.position1
        eps = 0.01
        dt=0.001
        T=1000
        t = time.perf_counter()
        for i in range(T):
            goalPosition0 = (i/T) * p0 + (1 - i/T) * p0_start
            goalPosition1 = (i/T) * p1 + (1 - i/T) * p1_start
            self.transfer() #transfer
            self.refCurrent0 = 1.0*(goalPosition0-self.position0)-0.1*self.velocity0
            self.refCurrent1 = 1.0*(goalPosition1-self.position1)-0.1*self.velocity1
            #wait for next control cycle
            t +=dt
            while(time.perf_counter()-t<dt):
                pass
        self.refCurrent0 = 0
        self.refCurrent1 = 0
        self.transfer()
  def stop(self):
        self.EI1OC = 0
        self.EI2OC = 0
        self.refPosition0 = 0
        self.refPosition1= 0
        self.refVelocity0= 0
        self.refVelocity1= 0
        self.refCurrent0= 0
        self.refCurrent1= 0
        self.iSatCurrent0= 0
        self.iSatCurrent1= 0
        self.kp0= 0
        self.kp1= 0
        self.kd0= 0
        self.kd1= 0
        self.timeout = 0
        dt=0.001
        t = time.perf_counter()
        for i in range(100):
            self.transfer() #transfer
            #wait for next control cycle
            t +=dt
            while(time.perf_counter()-t<dt):
                pass
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
